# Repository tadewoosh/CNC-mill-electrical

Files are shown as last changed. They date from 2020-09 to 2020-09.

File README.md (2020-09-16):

# CNC router/mill: electrical
The electrical part of the CNC router/mill project.

This repo contains the files needed for construction of a custom motion controller **based on the [GRBL 1.1](https://github.com/gnea/grbl) project**. If you don't want to make your own PCB you can use any GRBL-compatible motion controller - same basic principles of operation will apply.

## Table of contents
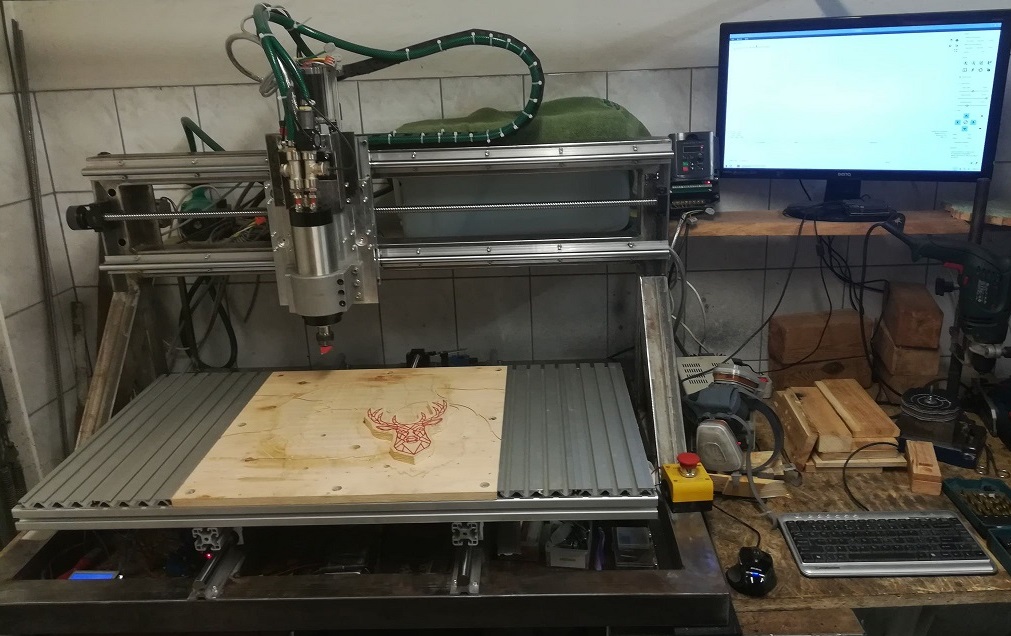
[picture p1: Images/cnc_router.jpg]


  * [Block diagram](#block-diagram)
  * [Motion controller](#motion-controller)
    + [Why not Arduino?](#why-not-arduino-)
    + [Detailed specification](#detailed-specification)
    + [GRBL Settings](#grbl-settings)
  * [Inputs wiring](#inputs-wiring)
    + [Limit switches](#limit-switches)
    + [Probe](#Probe)
    + [User buttons](#user-buttons)
  * [Motor Drivers](#motor-drivers)
    + [Driver configuration](#driver-configuration)
    + [Driver connection](#driver-connection)
  * [Inverter and Spindle](#inverter-and-spindle)
    + [Inverter connection](#inverter-connection)
    + [Spindle cooling](#spindle-cooling)
  * [Software for G-Code streaming](#software-for-g-code-streaming)
    + [Candle](#candle)
    + [GRBL Panel](#grbl-panel)

## Block diagram

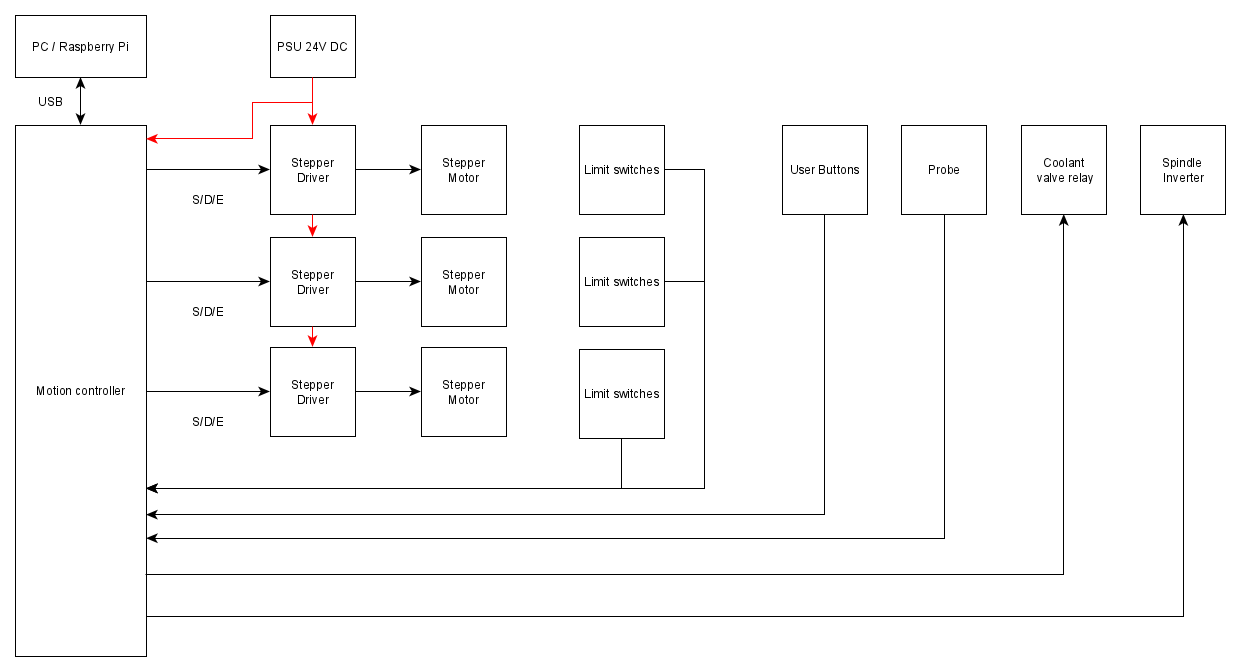
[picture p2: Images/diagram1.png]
diagram1


## Motion controller

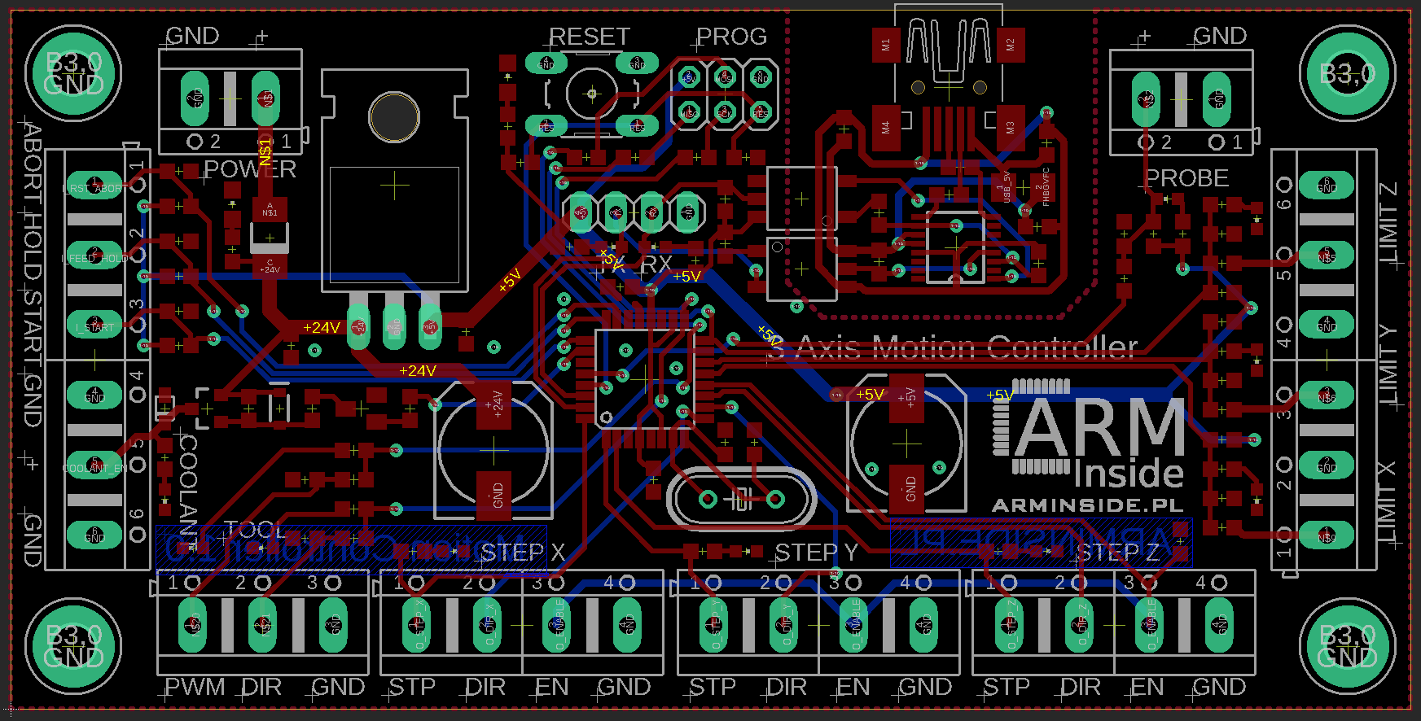
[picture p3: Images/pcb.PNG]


### Why not Arduino?
The main controller board is an AVR **ATmega8** based device aiming to replace the Arduino board as the motion controller. The reason why one might want to use this board instead of Arduino is that it provides:
* Galvanic insulation of the machine and the PC
* Robust power circuitry
* Robust, edge mounted connectors suitable for more "industrial" use
* Additional noise-reducing and LPF circuitry for the inputs and outputs
* A high-voltage output for the coolant valve relay

The Eagle project files are hosted in this repository along with the CAM configuration and its output (GERBER, drillfiles etc.) allowing for the easy PCB manufacturing/ordering.

In order to program a blank AVR chip with GRBL one needs first to obtain the Arduino bootloader allowing to update the frmware via the serial port from Arduino IDE.

### Detailed specification

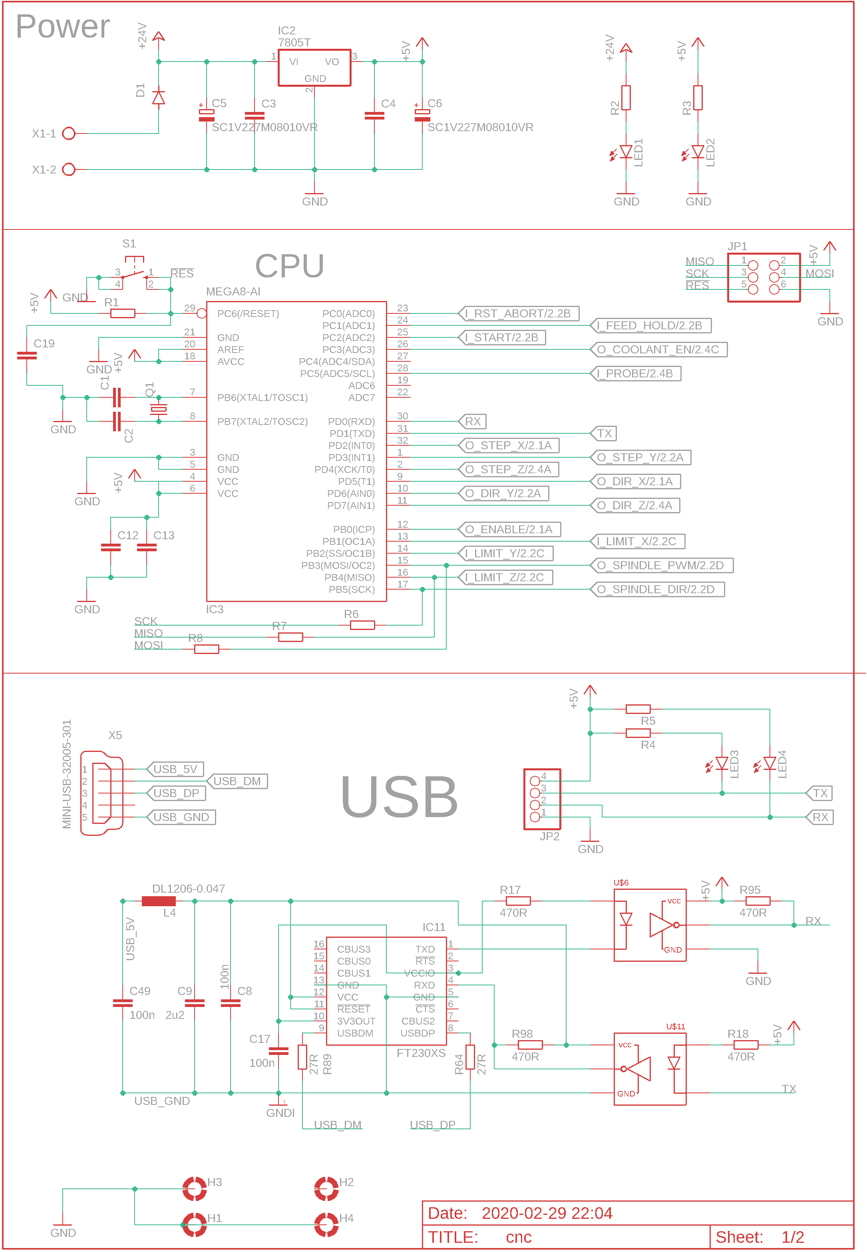
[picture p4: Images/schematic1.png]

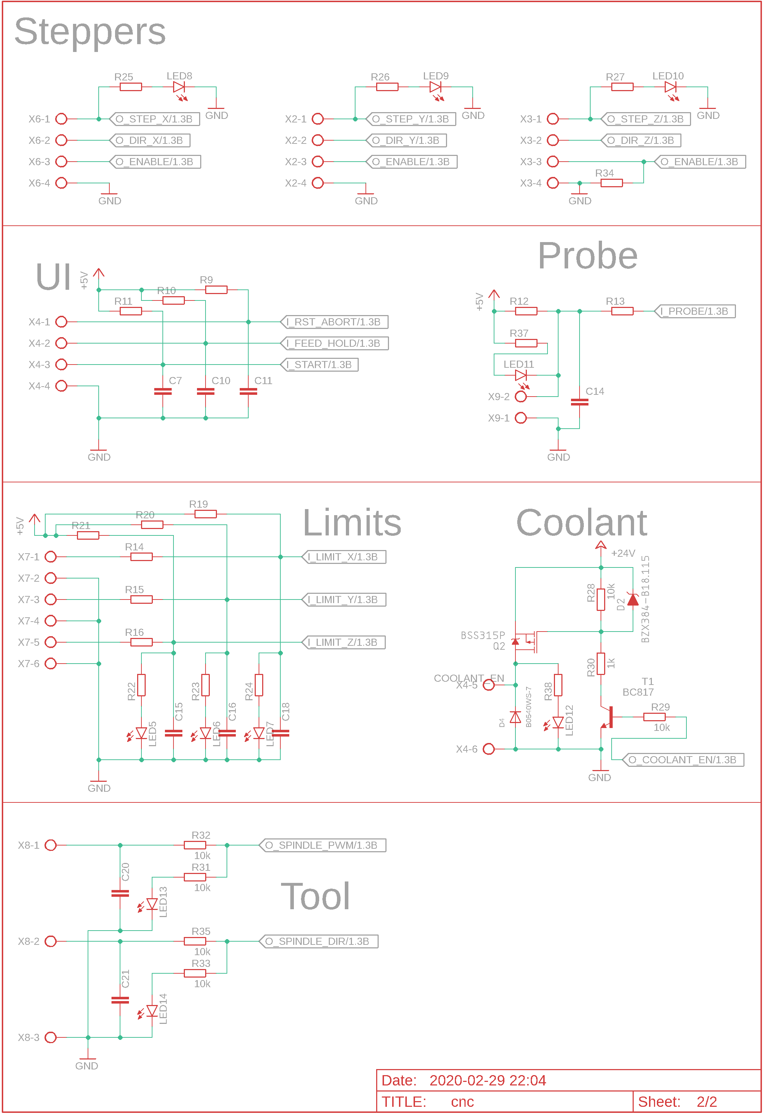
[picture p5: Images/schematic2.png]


* Up to 36V DC supply voltage when using **TSR 1-2450** DC-DC, otherwise **7805** linear regulator specification applies.
* Reverse power supply protection
* Reset switch
* ISP connector (*NOTE: Programming using ISP shlud not be conducted when the spindle inverter is connected.*)
* Debug serial commincation port with 5V tap
* USB to serial converter based on FTDI with optoisolation
* 3 sets of STEP/DIR/ENABLE connectors for stepper drivers with LED indicators
* User switches inputs (active low, with debouncing circuitry): ABORT, HOLD, START
* Probe input with debouncing circuitry and LED indication
* 3 limit switches inputs, active low, with debouncing circuitry and LED indication
* High voltage (supply), high current (1A) output for driving the coolant relay with Shottky protection (for the control of the tool cooling - rarely used for woodworking)
* PWM or analog (using LPF) 0-5V output for spindle speed and direction control with LED indication
* Simple and easy to hand-solder 100x50 mm two-layer board with 3mm holes in the corners for ease of mounting. 

### GRBL Settings
TODO: 

GRBL Settings

## Inputs wiring
### Limit switches
TODO:

Limit switches wiring

### Probe
TODO:

Probe wiring

### User buttons
TODO:

User Buttons wiring

## Motor Drivers
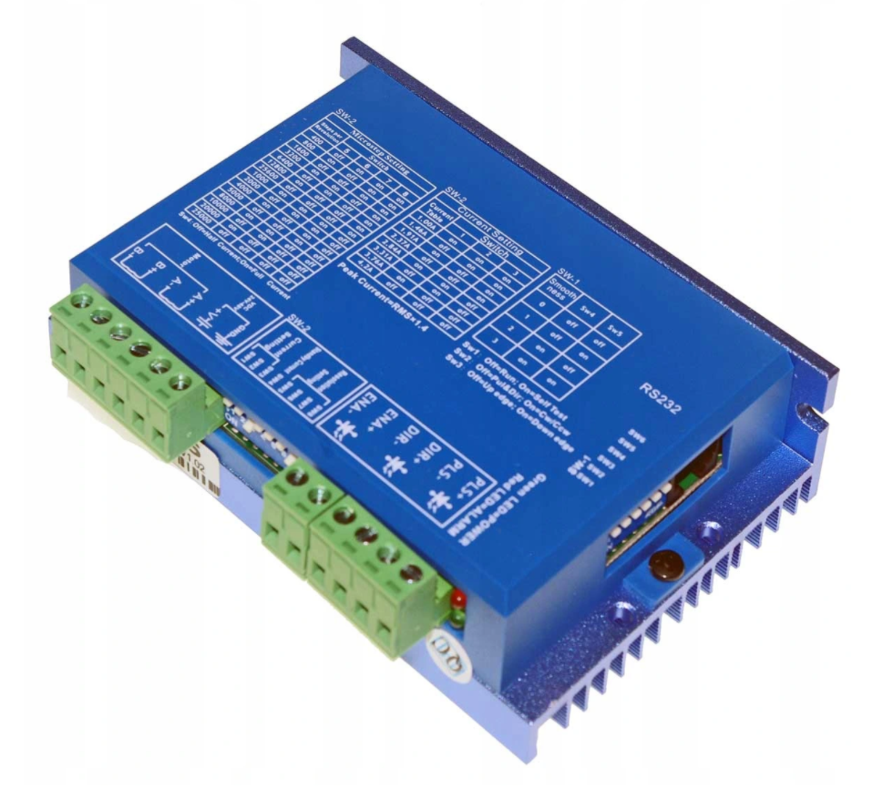
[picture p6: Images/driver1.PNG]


The **2DM556S** 4.2A RMS drivers are used.

### Driver configuration

* Current limiter on the driver is set to 3,31A in order to drive the **60HS100-3504A08-D24** 4,3N.m stepper motors. This is not the maximum current (3.5A) for the motors, but in order to keep them from overheating during some long sessions this needed to be lowered.
* Microstepping is set to "4000 Steps per revolution" accoding to the chineese maunfacturer. In real world combined with 1,8 sdegree mechanical resolution of the stepper and 5mm/turn of the ballscrew on each axis returns a resolution of 800 steps/mm. That means a theoretical resolution per step is 1.25 um which is absurd, yet it probably helps a bit with the smoothnes.
* Standby current is set, so when the motor is not in motion the current is lowered. This helps with overheating and I have not seen any adverse effects on the quality of the cuts.
* Smoothnes settings seem not to affect the operation nor the sound at all so I have turned it off. The speed ramps are calculated in the motion controller and they work OK. 

### Driver connection
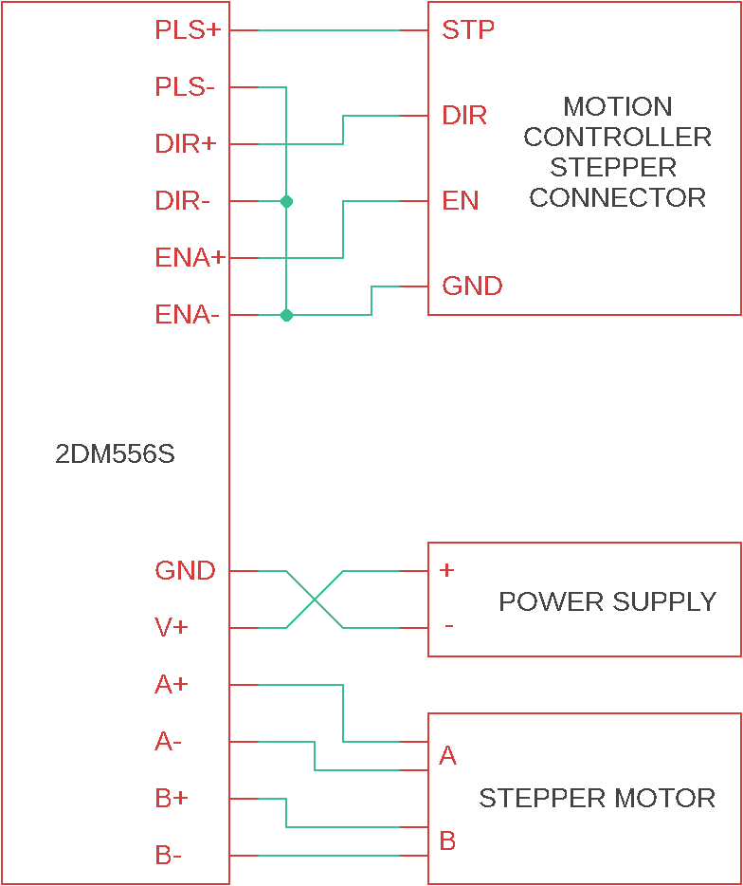
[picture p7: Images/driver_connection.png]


The cabling connecting all the low-power signals from motion controller to the driver should be as short as possible. Shielding and grounding should be sound in order to avoid EMC interference with high-current lines. Pay special notice to the location of the inverter-to-spindle cable (which should be shielded in its own right) since it is the devil of such application. Calculate the correct cable diameters in order to reduce voltage drops on the high-current lines. 

The drivers heated up very slightly during prolonged operation, the passive cooling of their ribbed cases seems sufficient.

## Inverter and Spindle
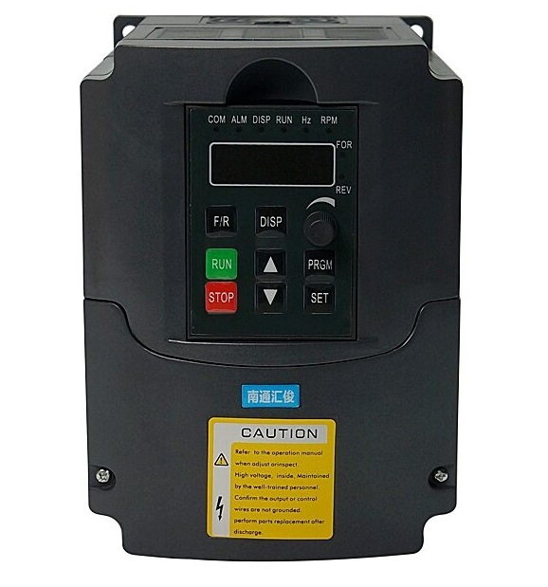
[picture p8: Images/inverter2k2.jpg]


A chineese set of inverter and spindle is used. The rated power of both is 2.2kW.

The inverter model is **YL620-A-2.2kW**. It is powered by a single-phase 230V mains.

### Inverter connection

TODO: 

Inverter Connection

### Spindle cooling
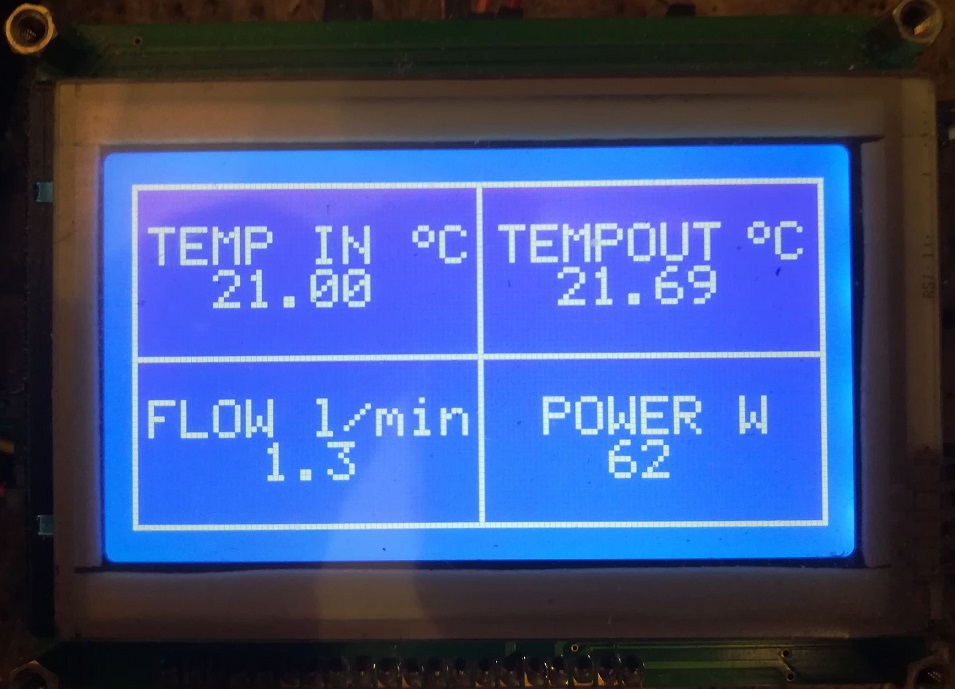
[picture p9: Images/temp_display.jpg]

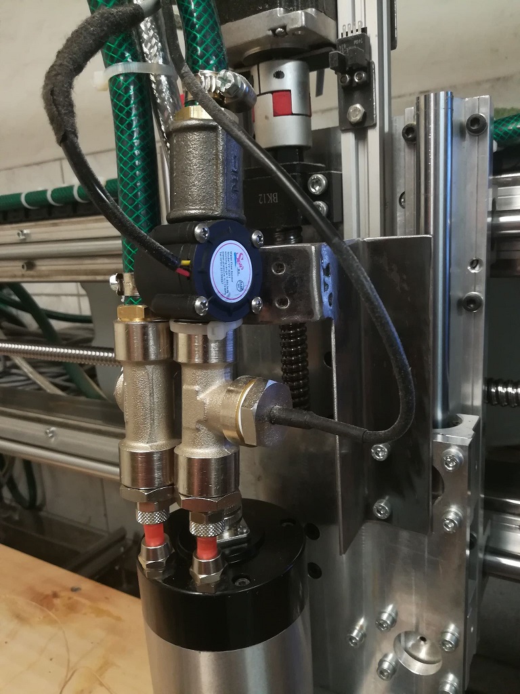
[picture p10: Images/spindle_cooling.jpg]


The spindle is water-cooled, so I made a temperature monitoring system from an old graphic-lcd project based on another AVR and here is what it does:
* measures the temperatures of the ingoing and outgoing coolant using **DS18B20** 1-wire digital thermometers
* measures the flow of the coolant using a simple **YF-S201** flow-meter
* calculates the thermal power gathered by the coolant
* displays calculated values live on the 128x64 LCD
* watches for ovearheat and low-flow conditions in order to alert the operator, pause the program and disable the spindle

## Software for G-Code streaming
### Candle
TODO:

Candle description

### GRBL Panel
TODO:

GRBL Panel description

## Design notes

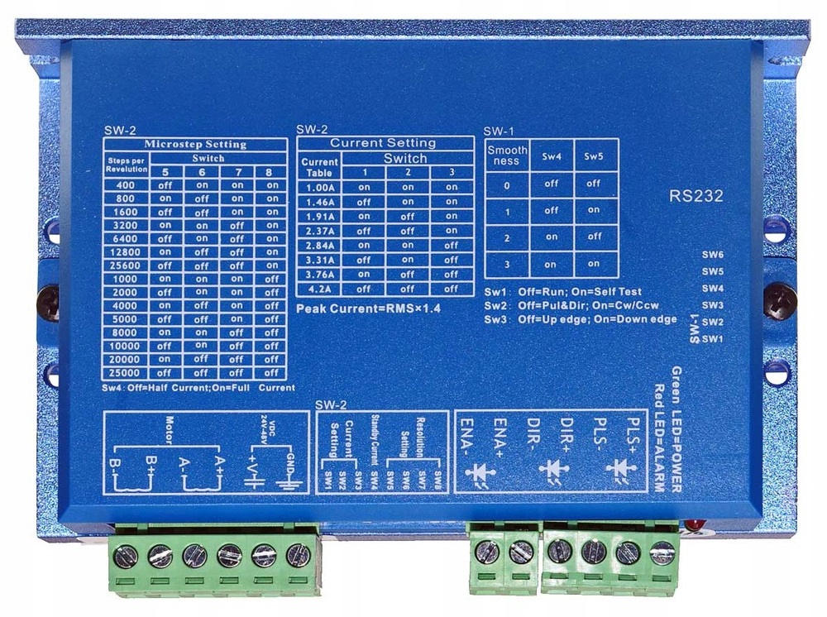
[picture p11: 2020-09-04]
Images/driver_top.jpg

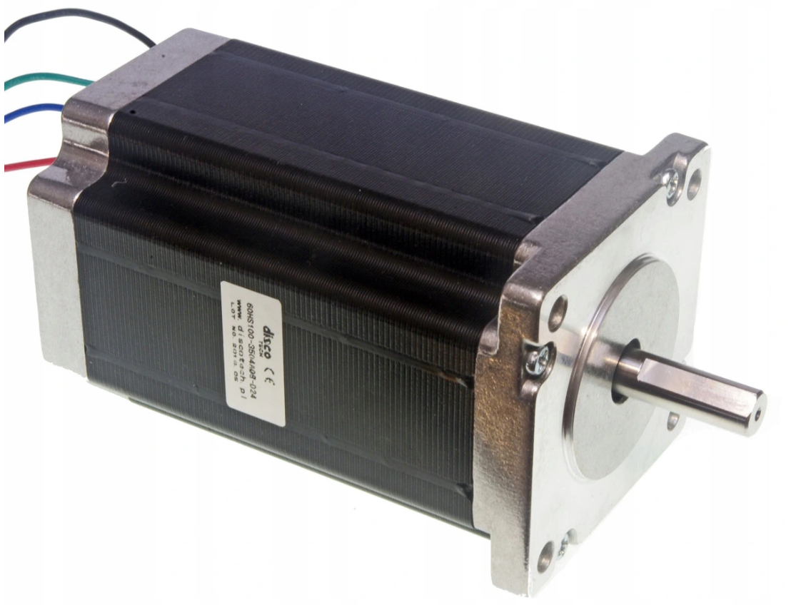
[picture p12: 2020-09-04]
Images/stepper1.PNG

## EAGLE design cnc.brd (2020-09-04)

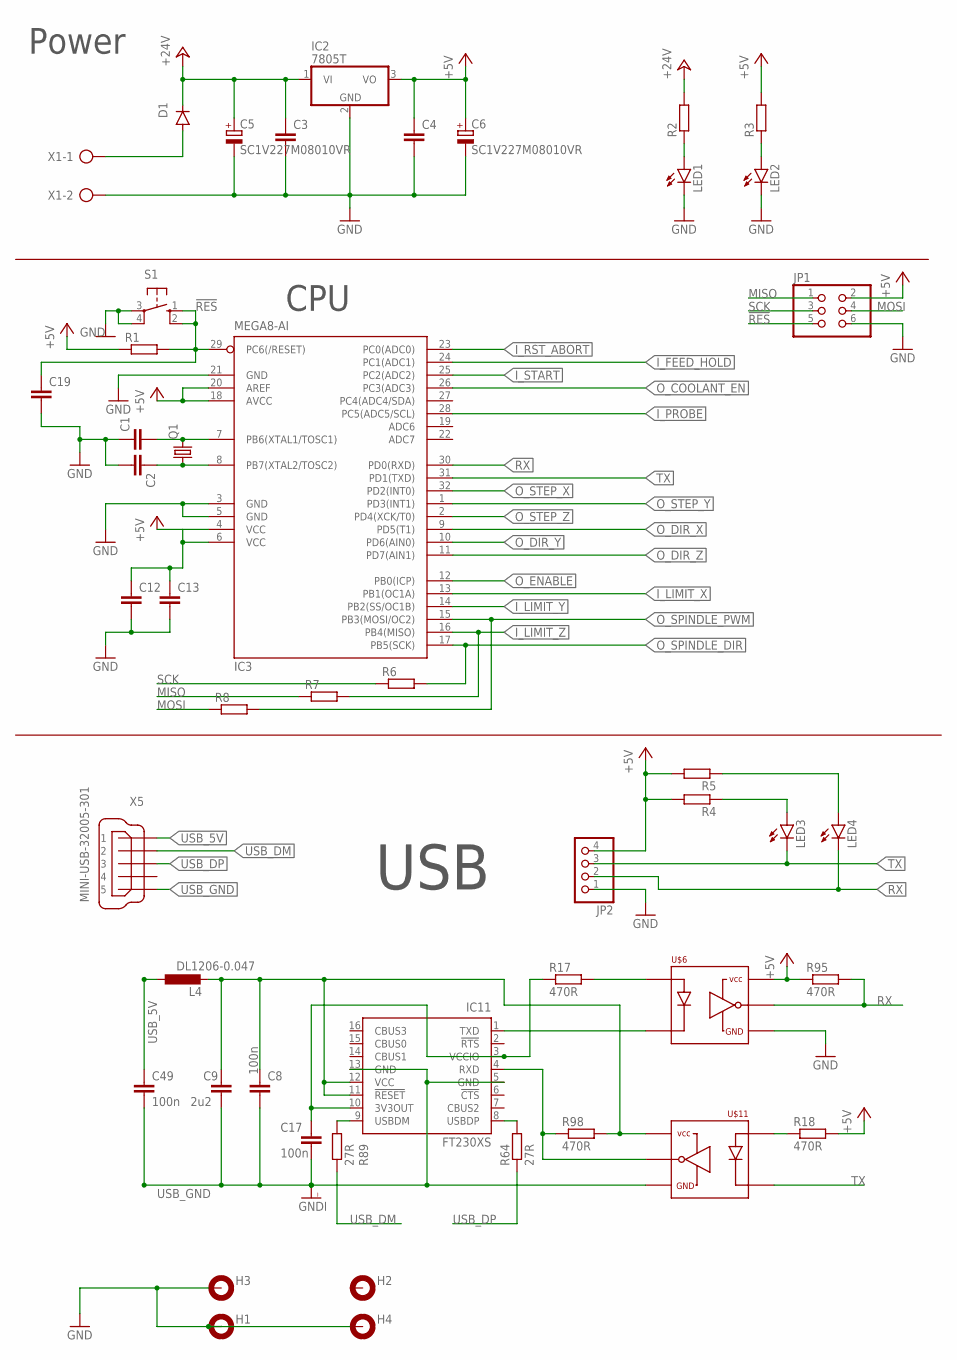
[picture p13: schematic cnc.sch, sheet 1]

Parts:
C1, C2, C3, C4, C12, C13, C19: C-EUC0603; C0603
C5, C6: SC1V227M08010VR; 150CLZ-0810
C8, C17, C49: 100n; C0603
C9: 2u2; C0603
D1: DIODE-DO-214AC; DO-214AC
H1, H2, H3, H4: MOUNT-PAD-ROUND3.0; 3,0-PAD
IC2: 7805T; TO220H
IC3: MEGA8-AI; TQFP32-08
IC11: FT230XS; SSOP16
JP1: PINHD-2X3; 2X03
JP2: PINHD-1X4; 1X04
L4: DL1206-0.047; L3225P
LED1, LED2: LEDCHIPLED_0805; CHIPLED_0805
LED3, LED4: LEDCHIPLED_0603; CHIPLED_0603
Q1: CRYSTALHC49S; HC49/S
R1, R2, R3, R4, R5, R6, R7, R8: R-EU_R0603; R0603
R17, R18, R95, R98: 470R; R0603
R64, R89: 27R; R0603
S1: 10-XX; B3F-10XX
U$6, U$11: TLP2362; SO-6
X1: AK500/2
X5: MINI-USB-32005-301; 32005-301

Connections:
!RES: C19.1, IC3.29 (PC6(/RESET)), JP1.5, R1.2, S1.1 (S), S1.2 (S1)
+5V: C4.1, C6.+, C12.1, C13.1, IC2.3 (VO), IC3.4 (VCC), IC3.6 (VCC), IC3.18 (AVCC), IC3.20 (AREF), JP1.2, JP2.4, R1.1, R3.2, R4.2, R5.2, R18.2, R95.1, U$6.6; also elsewhere on the board
+24V: C3.1, C5.+, D1.C, IC2.1 (VI), R2.2; also elsewhere on the board
FHBGVFC: C8.1, C9.1, IC11.11 (!RESET), IC11.12 (VCC), L4.2, R98.2, U$11.6
GND: C1.1, C2.2, C3.2, C4.2, C5.-, C6.-, C12.2, C13.2, C19.2, H1.B3,0, H3.B3,0, H4.B3,0, IC2.2 (GND), IC3.3 (GND), IC3.5 (GND), IC3.21 (GND), JP1.6, JP2.1, LED1.C, LED2.C, S1.3, S1.4 (P1), U$6.4, X1.2; also elsewhere on the board
I_FEED_HOLD: IC3.24 (PC1(ADC1)); also elsewhere on the board
I_LIMIT_X: IC3.13 (PB1(OC1A)); also elsewhere on the board
I_LIMIT_Y: IC3.14 (PB2(SS/OC1B)); also elsewhere on the board
I_LIMIT_Z: IC3.16 (PB4(MISO)), R7.2; also elsewhere on the board
I_PROBE: IC3.28 (PC5(ADC5/SCL)); also elsewhere on the board
I_RST_ABORT: IC3.23 (PC0(ADC0)); also elsewhere on the board
I_START: IC3.25 (PC2(ADC2)); also elsewhere on the board
MISO: JP1.1, R7.1
MOSI: JP1.4, R8.1
unnamed: D1.A, X1.1
unnamed: LED1.A, R2.1
unnamed: LED2.A, R3.1
unnamed: LED3.A, R4.1
unnamed: LED4.A, R5.1
unnamed: C1.2, IC3.7 (PB6(XTAL1/TOSC1)), Q1.2
unnamed: C2.1, IC3.8 (PB7(XTAL2/TOSC2)), Q1.1
unnamed: C17.1, IC11.3 (VCCIO), IC11.10 (3V3OUT), R17.1
unnamed: IC11.1 (TXD), U$6.3
unnamed: IC11.9 (USBDM), R89.2
unnamed: IC11.8 (USBDP), R64.2
unnamed: R17.2, U$6.1
unnamed: IC11.4 (RXD), R98.1, U$11.5
unnamed: R18.1, U$11.1
O_COOLANT_EN: IC3.26 (PC3(ADC3)); also elsewhere on the board
O_DIR_X: IC3.9 (PD5(T1)); also elsewhere on the board
O_DIR_Y: IC3.10 (PD6(AIN0)); also elsewhere on the board
O_DIR_Z: IC3.11 (PD7(AIN1)); also elsewhere on the board
O_ENABLE: IC3.12 (PB0(ICP)); also elsewhere on the board
O_SPINDLE_DIR: IC3.17 (PB5(SCK)), R6.2; also elsewhere on the board
O_SPINDLE_PWM: IC3.15 (PB3(MOSI/OC2)), R8.2; also elsewhere on the board
O_STEP_X: IC3.32 (PD2(INT0)); also elsewhere on the board
O_STEP_Y: IC3.1 (PD3(INT1)); also elsewhere on the board
O_STEP_Z: IC3.2 (PD4(XCK/T0)); also elsewhere on the board
RX: IC3.30 (PD0(RXD)), JP2.2, LED4.C, R95.2, U$6.5
SCK: JP1.3, R6.1
TX: IC3.31 (PD1(TXD)), JP2.3, LED3.C, U$11.3
USB_5V: C49.1, L4.1, X5.1
USB_DM: R89.1, X5.2
USB_DP: R64.1, X5.3
USB_GND: C8.2, C9.2, C17.2, C49.2, IC11.5 (GND), IC11.13 (GND), U$11.4, X5.5

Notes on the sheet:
Power
CPU
USB

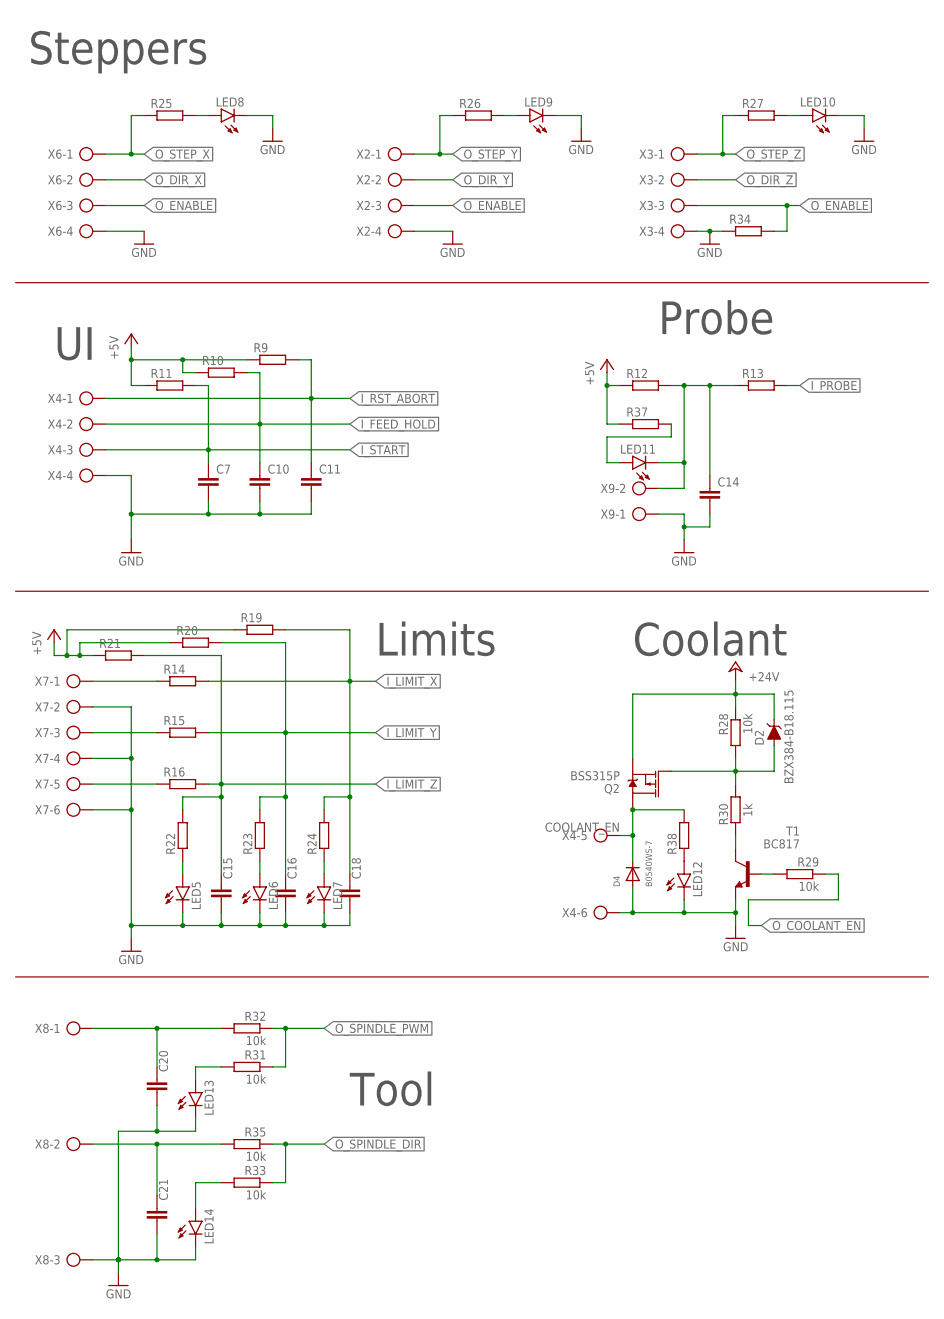
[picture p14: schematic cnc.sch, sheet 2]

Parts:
C7, C10, C11, C14, C15, C16, C18, C20, C21: C-EUC0603; C0603
D2: BZX384-B18.115; SOD-323
D4: B0540WS-7; SOD-323F
LED5, LED6, LED7, LED8, LED9, LED10, LED11, LED12, LED13, LED14: LEDCHIPLED_0603; CHIPLED_0603
Q2: BSS315P; SOT23-3
R9, R10, R11, R12, R13, R14, R15, R16, R19, R20, R21, R22, R23, R24, R25, R26, R27, R34, R37, R38: R-EU_R0603; R0603
R28, R29, R31, R32, R33, R35: 10k; R0603
R30: 1k; R0603
T1: BC817; SOT23-BEC
X2, X3, X6: AK500/4
X4, X7: AK500/6
X8: AK500/3
X9: AK500/2

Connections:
+5V: R9.1, R10.1, R11.1, R12.1, R19.1, R20.1, R21.1, R37.1; also elsewhere on the board
+24V: D2.C, Q2.2 (S), R28.1; also elsewhere on the board
COOLANT_EN: D4.C, Q2.3 (D), R38.2, X4.5
GND: C7.2, C10.2, C11.2, C14.2, C15.2, C16.2, C18.2, C20.2, C21.2, D4.A, LED5.C, LED6.C, LED7.C, LED8.C, LED9.C, LED10.C, LED12.C, LED13.C, LED14.C, R34.1, T1.E, X2.4, X3.4, X4.4, X4.6, X6.4, X7.2, X7.4, X7.6, X8.3, X9.1; also elsewhere on the board
I_FEED_HOLD: C10.1, R10.2, X4.2; also elsewhere on the board
I_LIMIT_X: C18.1, R14.2, R19.2, R24.2; also elsewhere on the board
I_LIMIT_Y: C16.1, R15.2, R20.2, R23.2; also elsewhere on the board
I_LIMIT_Z: C15.1, R16.2, R21.2, R22.2; also elsewhere on the board
I_PROBE: R13.2; also elsewhere on the board
I_RST_ABORT: C11.1, R9.2, X4.1; also elsewhere on the board
I_START: C7.1, R11.2, X4.3; also elsewhere on the board
unnamed: C14.1, LED11.C, R12.2, R13.1, X9.2
unnamed: R16.1, X7.5
unnamed: R15.1, X7.3
unnamed: R14.1, X7.1
unnamed: LED8.A, R25.2
unnamed: LED5.A, R22.1
unnamed: R30.2, T1.C
unnamed: LED6.A, R23.1
unnamed: LED9.A, R26.2
unnamed: LED7.A, R24.1
unnamed: LED14.A, R33.2
unnamed: LED13.A, R31.2
unnamed: LED10.A, R27.2
unnamed: C20.1, R32.2, X8.1
unnamed: C21.1, R35.2, X8.2
unnamed: LED11.A, R37.2
unnamed: LED12.A, R38.1
unnamed: D2.A, Q2.1 (G), R28.2, R30.1
unnamed: R29.2, T1.B
O_COOLANT_EN: R29.1; also elsewhere on the board
O_DIR_X: X6.2; also elsewhere on the board
O_DIR_Y: X2.2; also elsewhere on the board
O_DIR_Z: X3.2; also elsewhere on the board
O_ENABLE: R34.2, X2.3, X3.3, X6.3; also elsewhere on the board
O_SPINDLE_DIR: R33.1, R35.1; also elsewhere on the board
O_SPINDLE_PWM: R31.1, R32.1; also elsewhere on the board
O_STEP_X: R25.1, X6.1; also elsewhere on the board
O_STEP_Y: R26.1, X2.1; also elsewhere on the board
O_STEP_Z: R27.1, X3.1; also elsewhere on the board

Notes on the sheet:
Steppers
Limits
Tool
Coolant
Probe

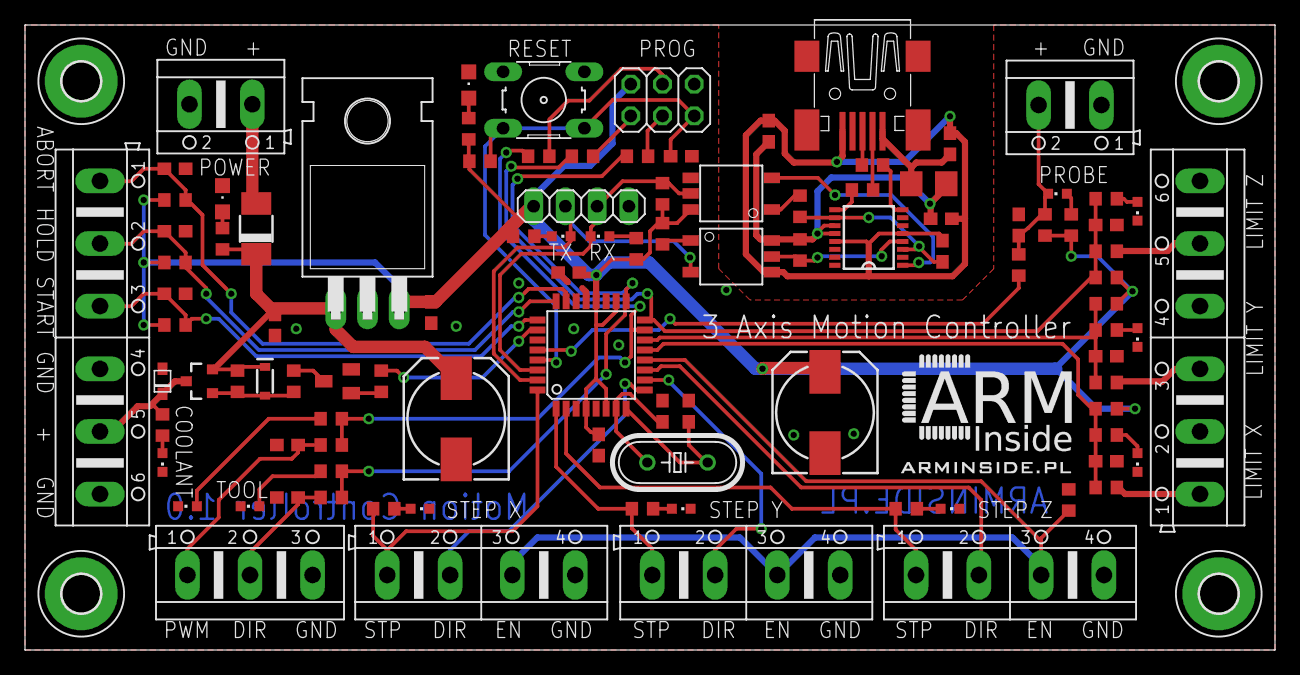
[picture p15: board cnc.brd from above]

Board: 2 copper layers, 100.0 x 50.0 mm, 105 parts (0 on the bottom side), 65 nets.

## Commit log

2020-09-04 CAM output
    [copper_bottom.gbr, copper_top.gbr, drill_1_16.xln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]
2020-09-04 driver connection

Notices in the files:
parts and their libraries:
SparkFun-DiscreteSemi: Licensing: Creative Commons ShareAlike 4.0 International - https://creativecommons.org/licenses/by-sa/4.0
